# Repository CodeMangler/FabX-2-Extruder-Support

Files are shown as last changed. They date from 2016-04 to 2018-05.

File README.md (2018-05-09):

# FabX-2-Extruder-Support

FabX 2 machines use a Budaschnozzle v2 (likely, a chinese variant of it), which is mounted a few mm below the extruder assembly. The gap causes flex filaments to, well, flex occasionally and make it hard to print with them.

This thing closes the gap between the extruder assembly and the hotend, providing a near gapless path for the filament to pass through. This support has been designed to be used with an additional PTFE (or similar) tubing (~14.2mm, OD 4mm by default) to provide a smoother path for the filament.

This is now available on Thingiverse at: http://www.thingiverse.com/thing:1472080

FabX 2 Extruder Support on Thingiverse

## How I Designed This
I made the initial version by measuring topside of the Budaschnozzle with a pair of calipers and then modelling based on that. It turned out to be fairly inaccurate.

For the second version, I found the Budaschnozzle v2.0 drawings published by Lulzbot (https://devel.lulzbot.com/Budaschnozzle/v2.0/), which helped fixed the dimensions to an extent. I made a drawing in AutoCAD and then extruded it to get the final 3D shape. This turned out pretty well, except it needed a bit of dremelling at the corners to make it fit properly.

I made the third version from scratch in OpenSCAD, based on the official Budaschnozzle drawing. This fits well enough at the bottom (against the screws), but may need a bit of dremelling at the top to better fit against the extruder gear and idler. If it doesn't fit well, it should be easy to modify it since it's an OpenSCAD model.

Version four has additional grooves to better fit with the extruder gear and the idler, and some customizations specific to my machine, which has a PTFE tube that protrudes out of the hotend.

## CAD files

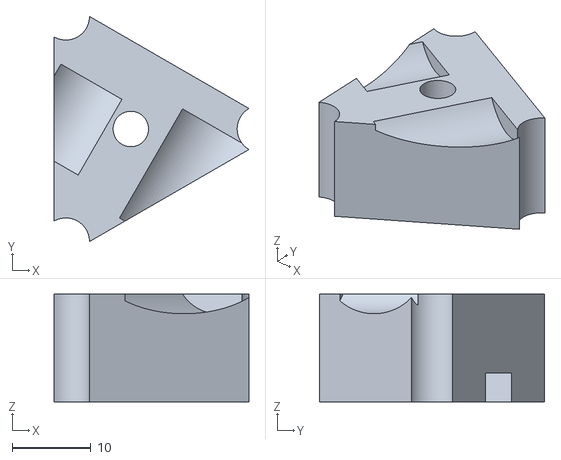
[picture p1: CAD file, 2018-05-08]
v4/FabX 2 Extruder Support v4.stl
24.8 x 28.6 x 13.7

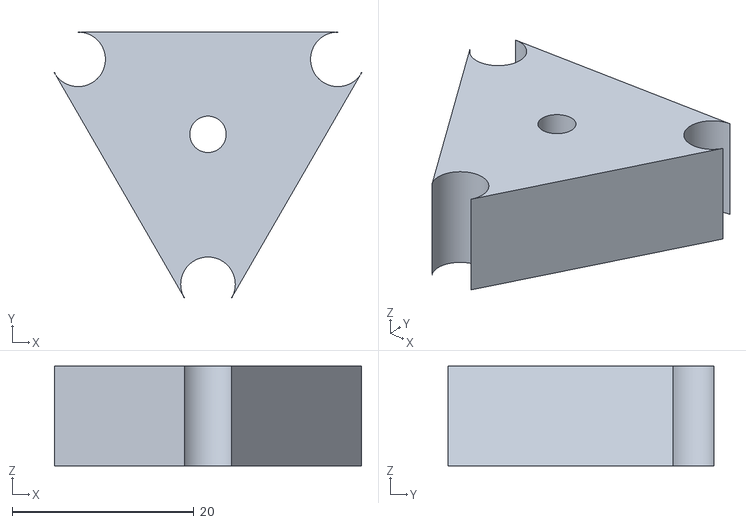
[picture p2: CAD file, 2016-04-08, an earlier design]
v2/FabX 2 Extruder Support v2.stl
33.8 x 29.2 x 11.0

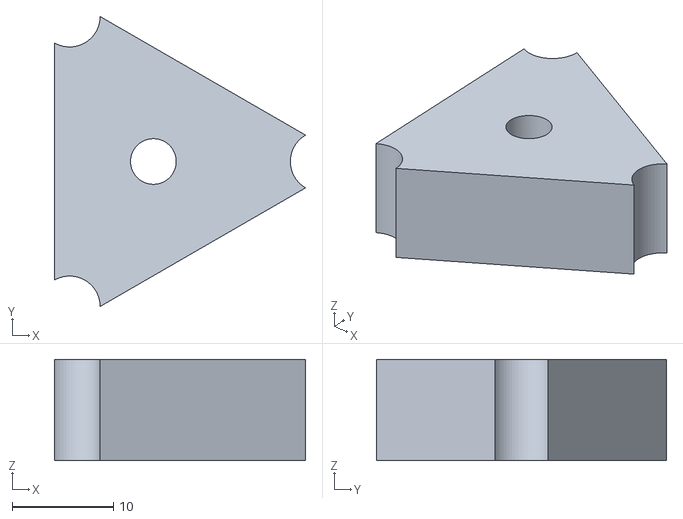
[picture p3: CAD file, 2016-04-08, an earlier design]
v3/FabX 2 Extruder Support v3.stl
24.8 x 28.6 x 10.0

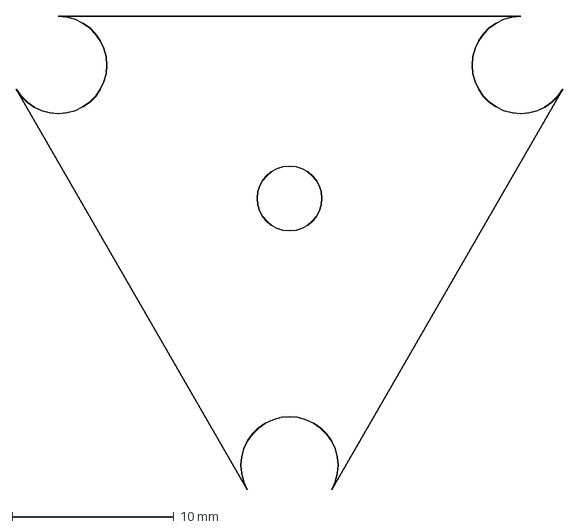
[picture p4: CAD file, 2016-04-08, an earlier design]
v2/FabX 2 Extruder Support v2 - Ungrouped.dxf
33.8 x 29.2 mm

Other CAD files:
v4/FabX 2 Extruder Support v4.scad
v3/FabX 2 Extruder Support v3.scad
v2/FabX 2 Extruder Support v2.dwg
v2/FabX 2 Extruder Support v2.dxf

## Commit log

2016-04-08 Initial commit - v2 drawings and STL
    [FabX 2 Extruder Support v2 - Ungrouped.dxf, FabX 2 Extruder Support v2.dwg, FabX 2 Extruder Support v2.dxf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]
2016-04-08 Redesigned the part using OpenSCAD - Uses parameter values from the official Budaschnozzle Upper Plate drawing
    [FabX 2 Extruder Support v3.scad, FabX 2 Extruder Support v3.stl]
2018-05-07 [v4] Update support block to also hold the hotend PTFE protrusion
    [FabX 2 Extruder Support v4.scad, FabX 2 Extruder Support v4.stl]
2018-05-08 [v4] Adjust dimensions and carve out grooves for better fit
    - Add groove to allow sliding in over the hotend PTFE protrusion
    - Add grooves to fit the extruder gear and idler
    [FabX 2 Extruder Support v4.scad, FabX 2 Extruder Support v4.stl]
